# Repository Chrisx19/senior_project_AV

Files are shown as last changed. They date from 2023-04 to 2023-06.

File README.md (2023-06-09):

# CPP Senior Project
Senior project

## December 2022 - May 2023
ROS Noetic control GPS autonomous vehicle using ATMega2560 and Jetson Nano. 

## Video Demo
**Autonomous Mode:**        https://youtu.be/Os8QsEWLSAU

**Controller Mode:**        https://youtu.be/IqCc2zWrYO0

**Test Controller Mode:**   https://youtu.be/60IaMCZQ1AA

### Mechanical 


### Electrical

**PCB Design**
  Reason initial design is included because of the mistakes my team learned while testing. Due to small traces with about 3 Amps going inside of our traces, it blew up and it came out of the PCB. Therefore, we learned from mistakes and calculated how much mil we need for our traces that can withstand about 4 Amps.
  
* **Initial Design: 30 mil traces**



* **Final Design: 150 mil traces**

schematic

Traces

### Software 
* **Communication:** 
  In order to have Jetson Nano and ATMega2560 talk to each other bi directionally, we used a customed UART protocol from ROS package called 'Rosserial.' Rosserial protocol was able to give us the ncecesity we need to transfer data from each other while autonomy. With rosserial, ATMega2560 became its own node and Jetson Nano has its main node and sub node. Nodes are basically scripts, which transfer myriad of data types from node to node.

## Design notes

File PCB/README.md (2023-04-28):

# PCB Design Final


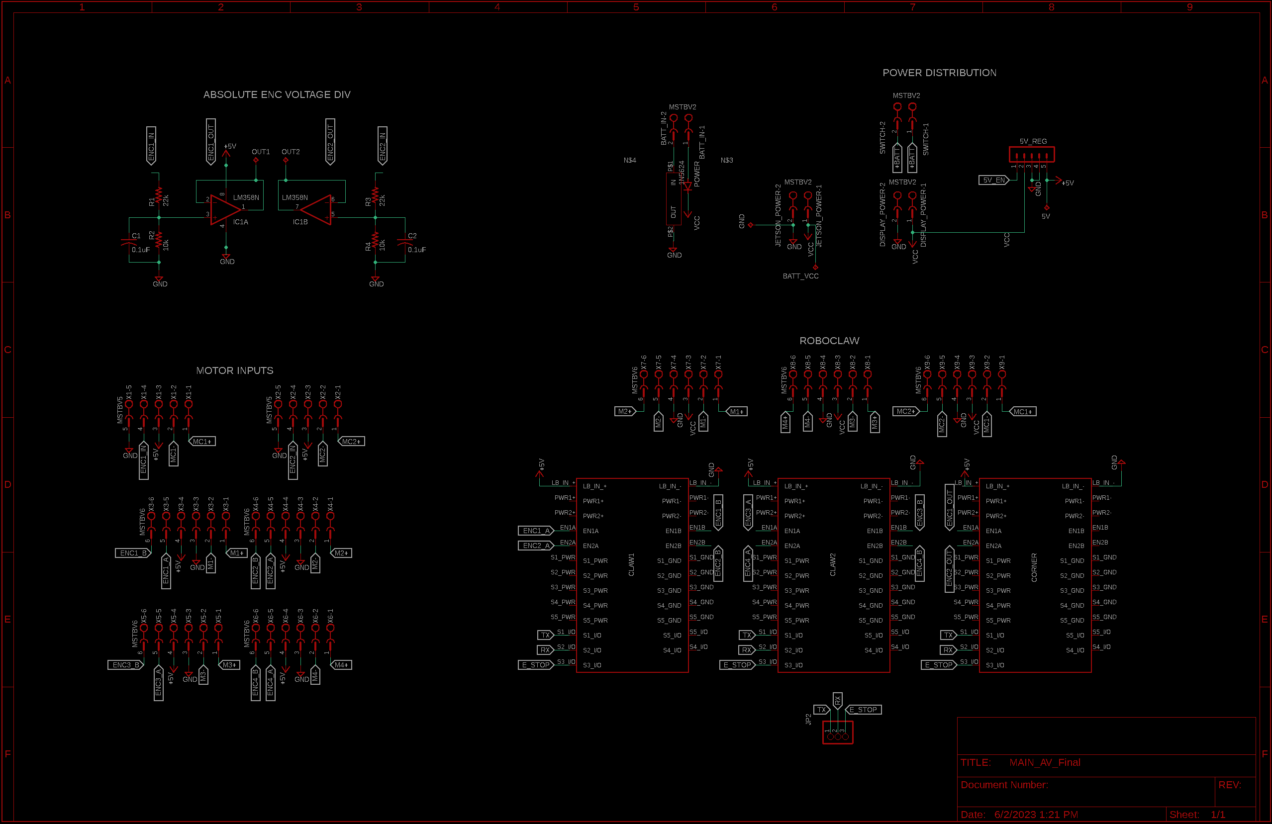
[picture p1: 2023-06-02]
Pictures/schematic.png

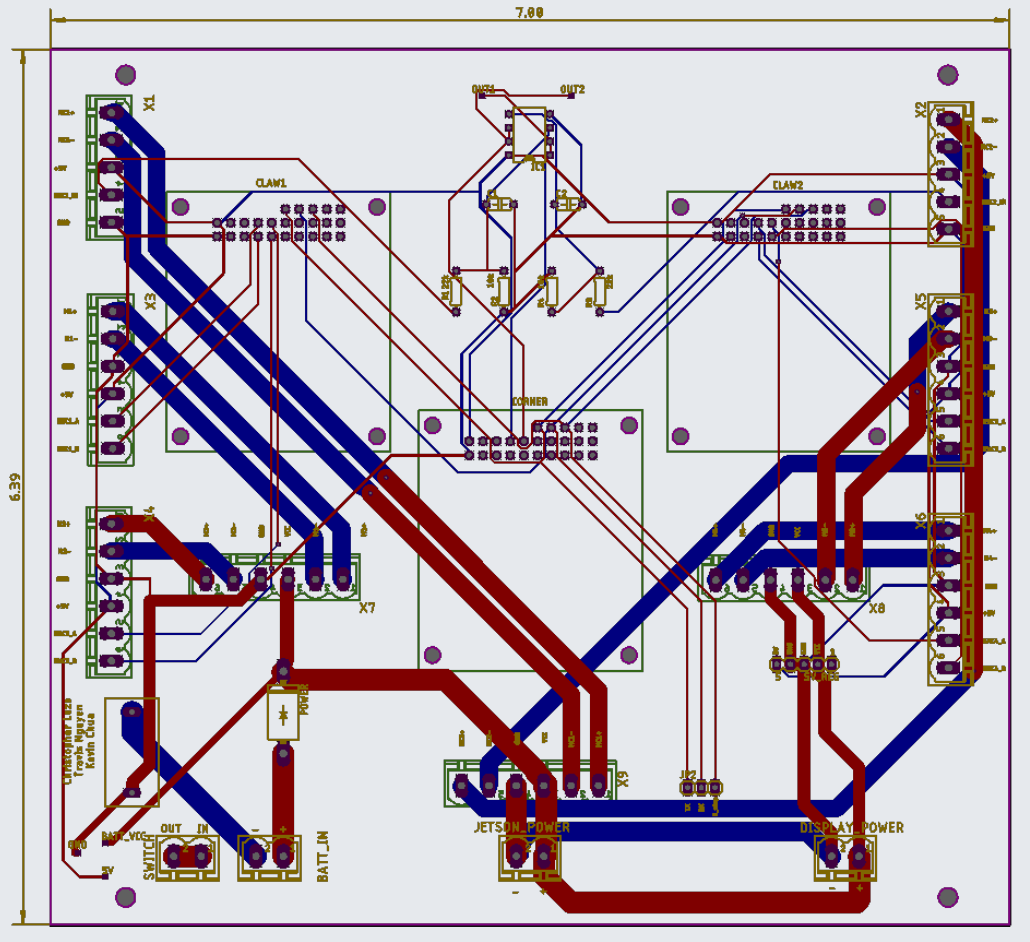
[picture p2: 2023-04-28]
Pictures/Traces.PNG

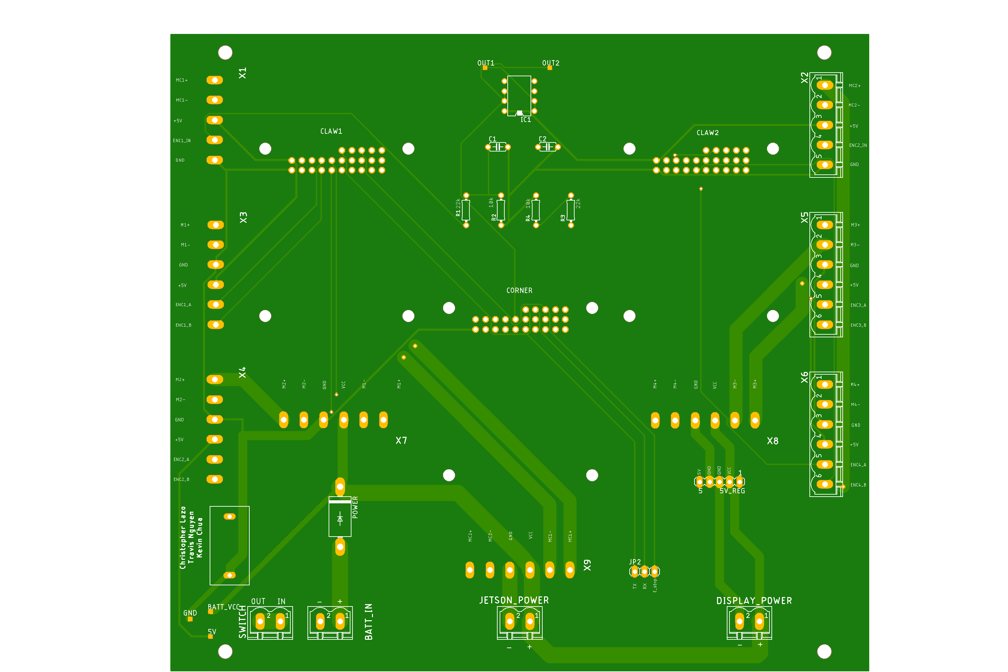
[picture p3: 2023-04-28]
Pictures/Final_Board.png

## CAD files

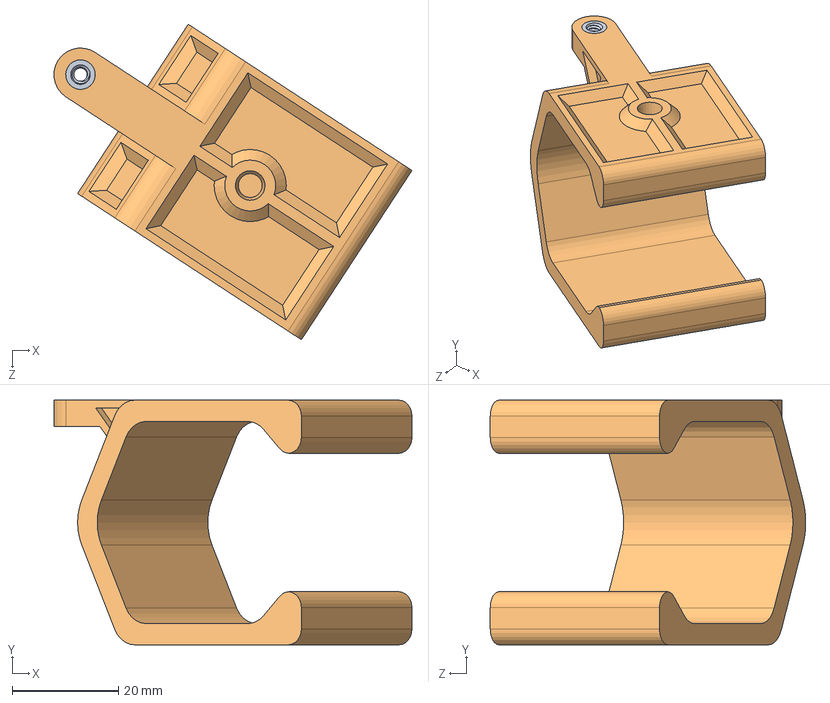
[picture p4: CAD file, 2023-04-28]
Mechanical/Body_senior/3d_printed/Battery holder_5_2mAH.SLDASM
67.3 x 46.0 x 59.3 mm
93365A130_HEAT-SET INSERTS FOR PLASTICS
battery holder_5_2maH

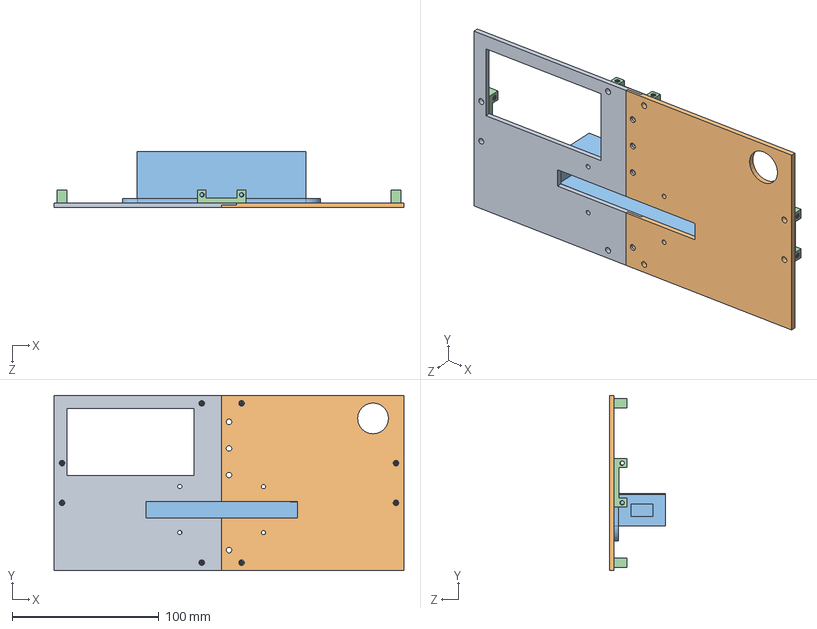
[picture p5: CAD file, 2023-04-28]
Mechanical/Full_Car.SLDASM
238.3 x 119.4 x 38.2 mm
Half_Left_Back
Half_Right_Back
USB_hub_mount
Dual Side Mount_Plate.step x 4

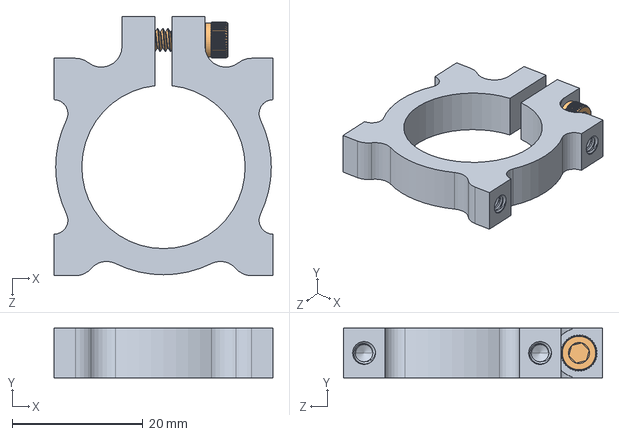
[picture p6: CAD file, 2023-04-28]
Mechanical/wheel_senior/25m Bore Side Tapped Clamping Mount.SLDASM
33.5 x 7.62 x 39.7 mm
25m Bore Side Tapped Clamping Mount
#6-32 0_5 Bolt

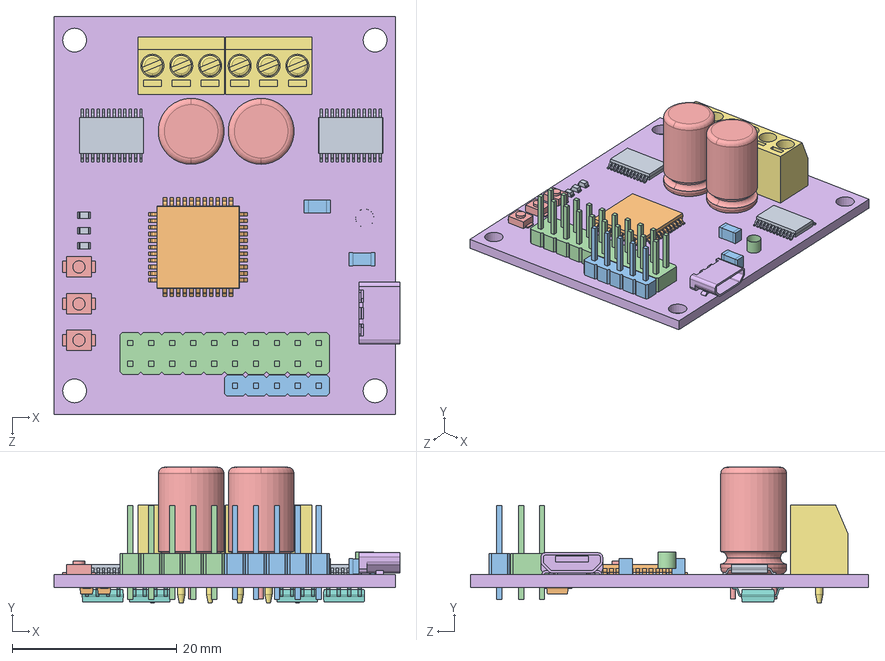
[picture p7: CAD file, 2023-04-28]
Mechanical/Body_senior/electronics/Roboclaw.SLDASM
42.0 x 16.5 x 48.3 mm
404-1004-1-ND x 3
DB2W40200LCT-ND x 2
587-3248-1-ND x 2
SRN5040-220MCT-ND
P15369TB-ND x 2
609-4618-1-ND
ED2636-ND x 2
IRF7351TRPBFCT-ND x 4
620-1319-1-ND x 2
ATXMEGA32A4U-AU-ND
PBC05SAAN
PBC10DAAN
SW1020CT-ND x 3
MC5A-PCB

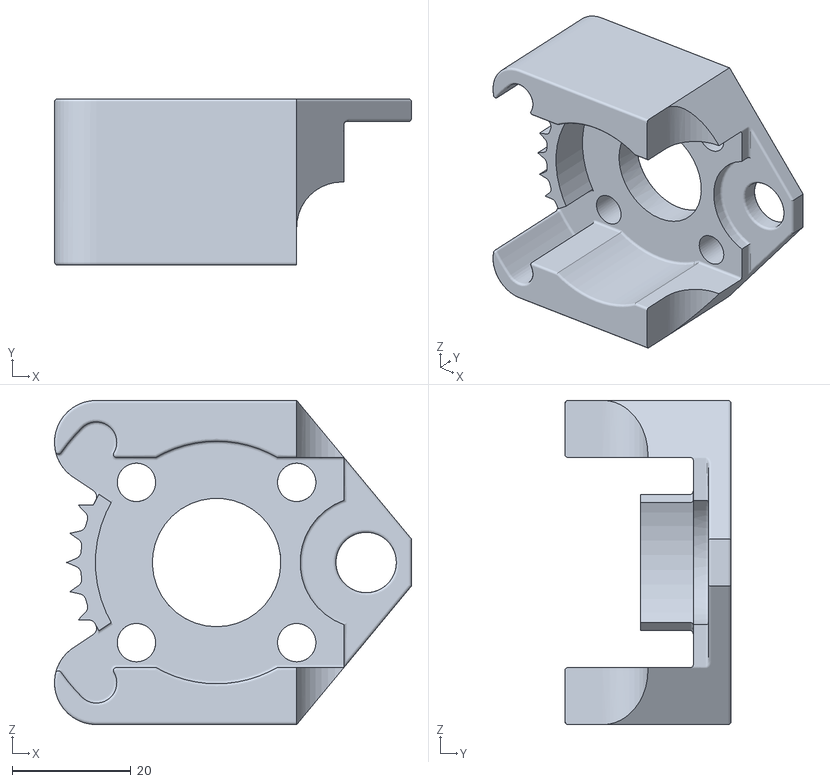
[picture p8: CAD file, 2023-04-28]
3D Parts/Encoder mount.STL
60.0 x 27.9 x 54.5

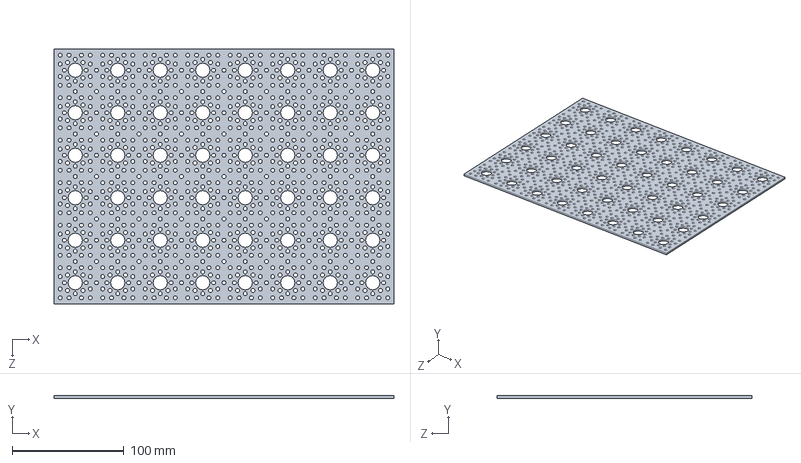
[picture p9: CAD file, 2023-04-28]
Mechanical/Body/9 x 12 Aluminum Pattern Plate.SLDPRT
304.8 x 2.29 x 228.6 mm

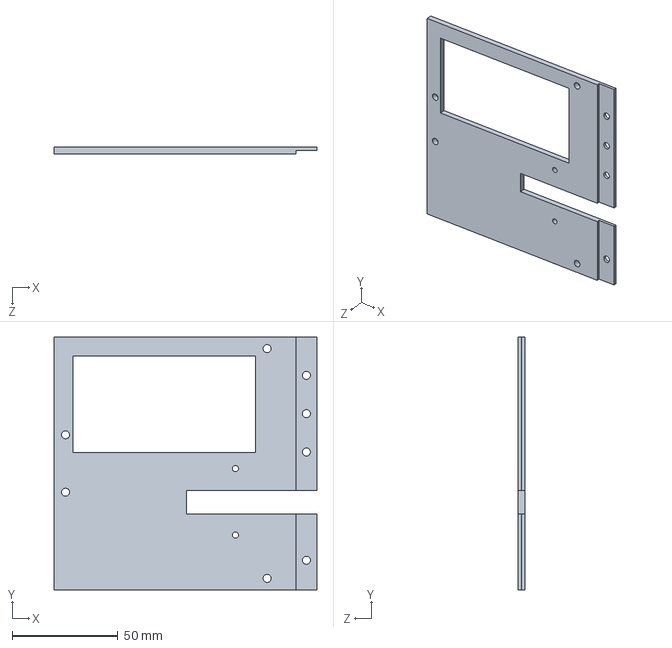
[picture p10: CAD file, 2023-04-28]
Mechanical/Body/Half_Left_Back.SLDPRT
124.2 x 119.4 x 3.17 mm

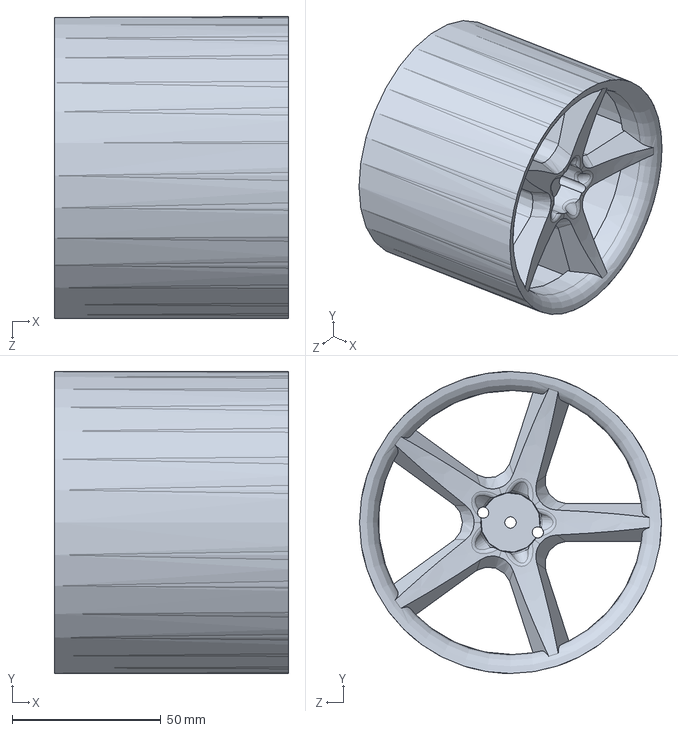
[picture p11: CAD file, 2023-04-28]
Mechanical/wheel_senior/Wheel Rim.sldprt
78.7 x 101.6 x 101.6 mm

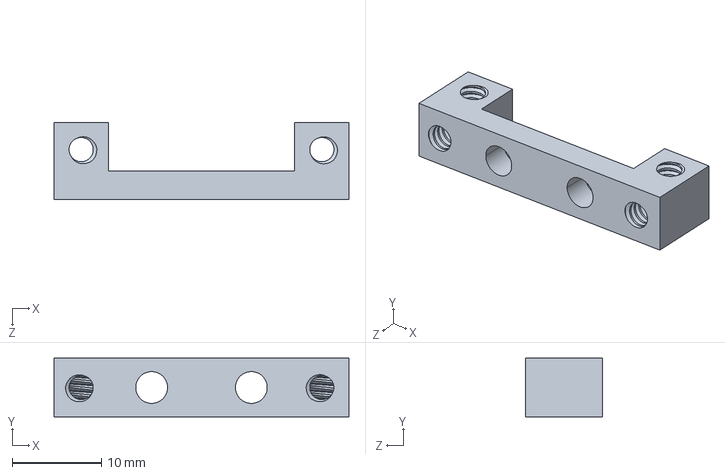
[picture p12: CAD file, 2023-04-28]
Mechanical/Body/Dual Side Mount_Plate.STEP
33.0 x 6.58 x 8.63 mm

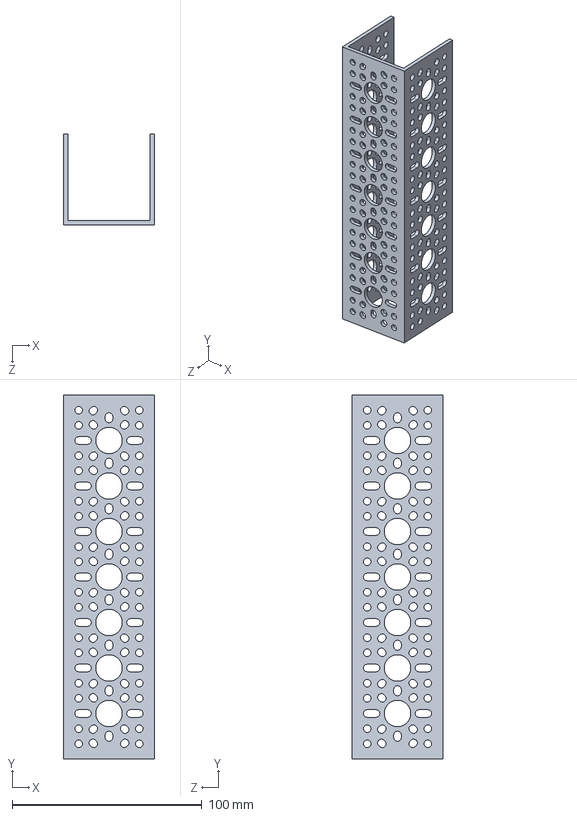
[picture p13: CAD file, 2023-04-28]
Mechanical/wheel_senior/gobilda-7hole-1120series-channel.SLDPRT
48.0 x 192.0 x 48.0 mm

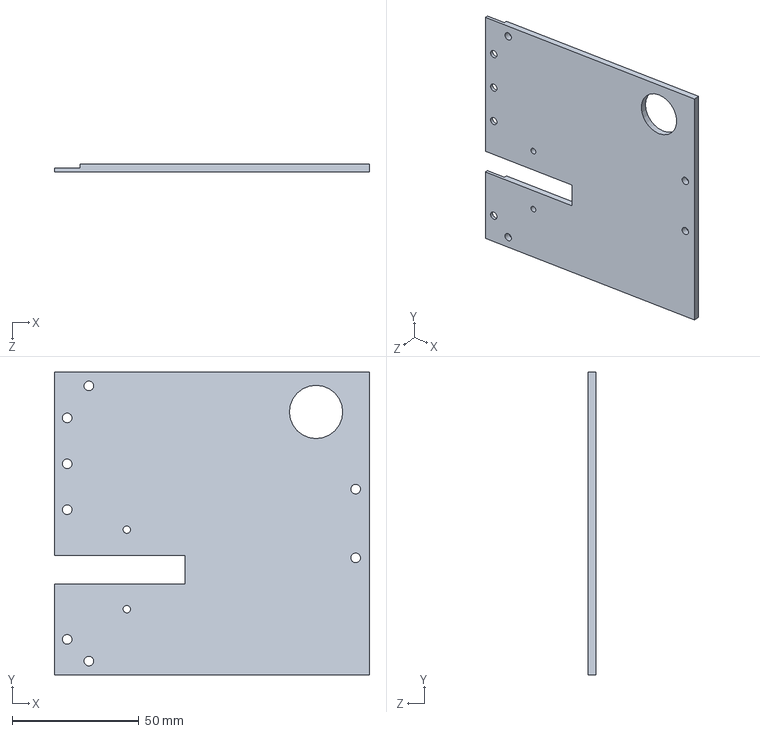
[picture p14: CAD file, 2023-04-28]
Mechanical/Body/Half_Right_Back.SLDPRT
124.2 x 119.4 x 3.18 mm

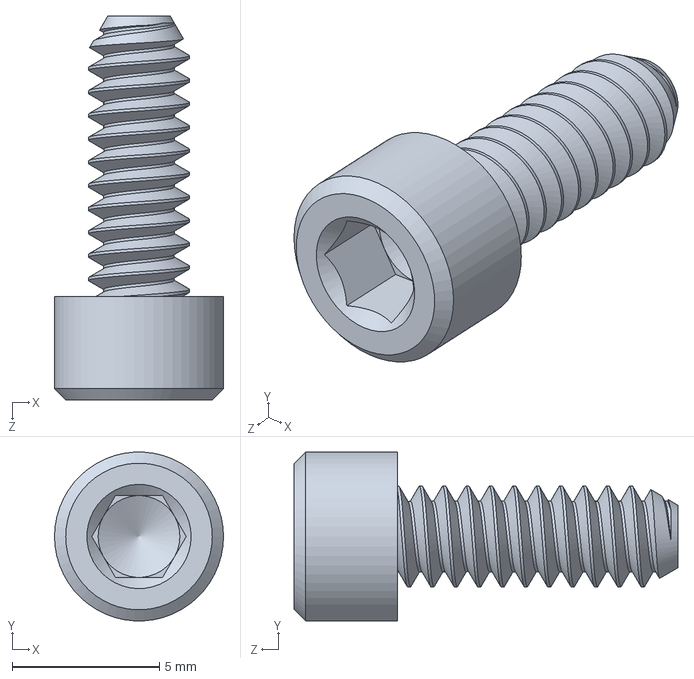
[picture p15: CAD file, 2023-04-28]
Mechanical/wheel_senior/6-32_SHCS.SLDPRT
5.74 x 5.73 x 13.0 mm

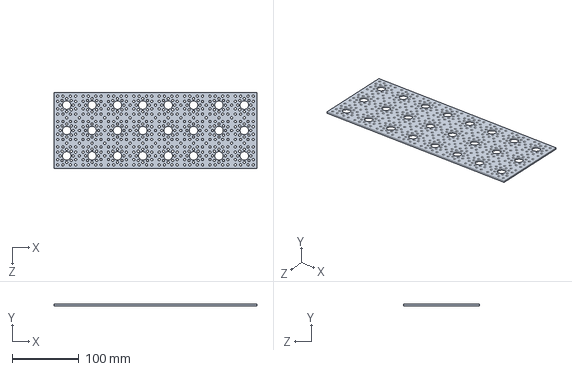
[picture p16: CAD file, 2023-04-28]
Mechanical/Body/4.5 x 12 Aluminum Pattern Plate.SLDPRT
304.8 x 2.29 x 114.3 mm

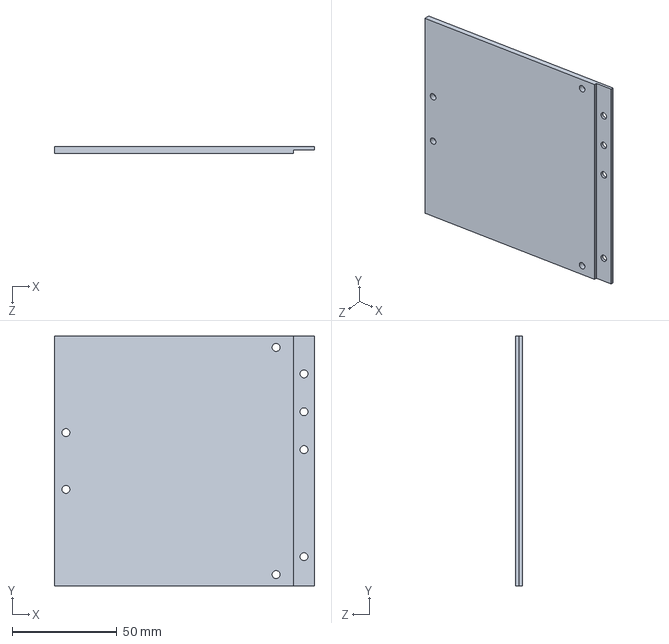
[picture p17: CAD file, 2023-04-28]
Mechanical/Body/Front_Panel_Right.SLDPRT
124.2 x 119.4 x 3.17 mm

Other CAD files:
Mechanical/Body_senior/electronics/SRN5040-220MCT-ND.sldprt
Mechanical/Body_senior/electronics/587-3248-1-ND.sldprt
Mechanical/Body_senior/electronics/DB2W40200LCT-ND.sldprt
Mechanical/Body_senior/electronics/609-4618-1-ND.sldprt
Mechanical/Body/Front_Panel_Left.SLDPRT
Mechanical/Body/Front_Panel_Left.STL
Mechanical/Body/Front_Panel_Right.STL
Mechanical/Body/Half_Left_Back.STL
Mechanical/Body/Half_Right_Back.STL
Mechanical/Body/USB_hub_mount.SLDPRT
Mechanical/Body/USB_hub_mount.STEP
Mechanical/Body/USB_hub_mount.STL
Mechanical/Body/back_panel.STEP
Mechanical/Body/back_panel.STL
Mechanical/Body/front_panel.STEP
Mechanical/Body/front_panel.STL
Mechanical/Body_senior/3d_printed/battery holder_5_2maH.SLDPRT
Mechanical/Body_senior/3d_printed/battery holder_5_2maH.STL
Mechanical/Body_senior/control_board/91255A077_ALLOY STEEL BUTTON-HEAD SOCKET CAP SCREW.SLDPRT
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

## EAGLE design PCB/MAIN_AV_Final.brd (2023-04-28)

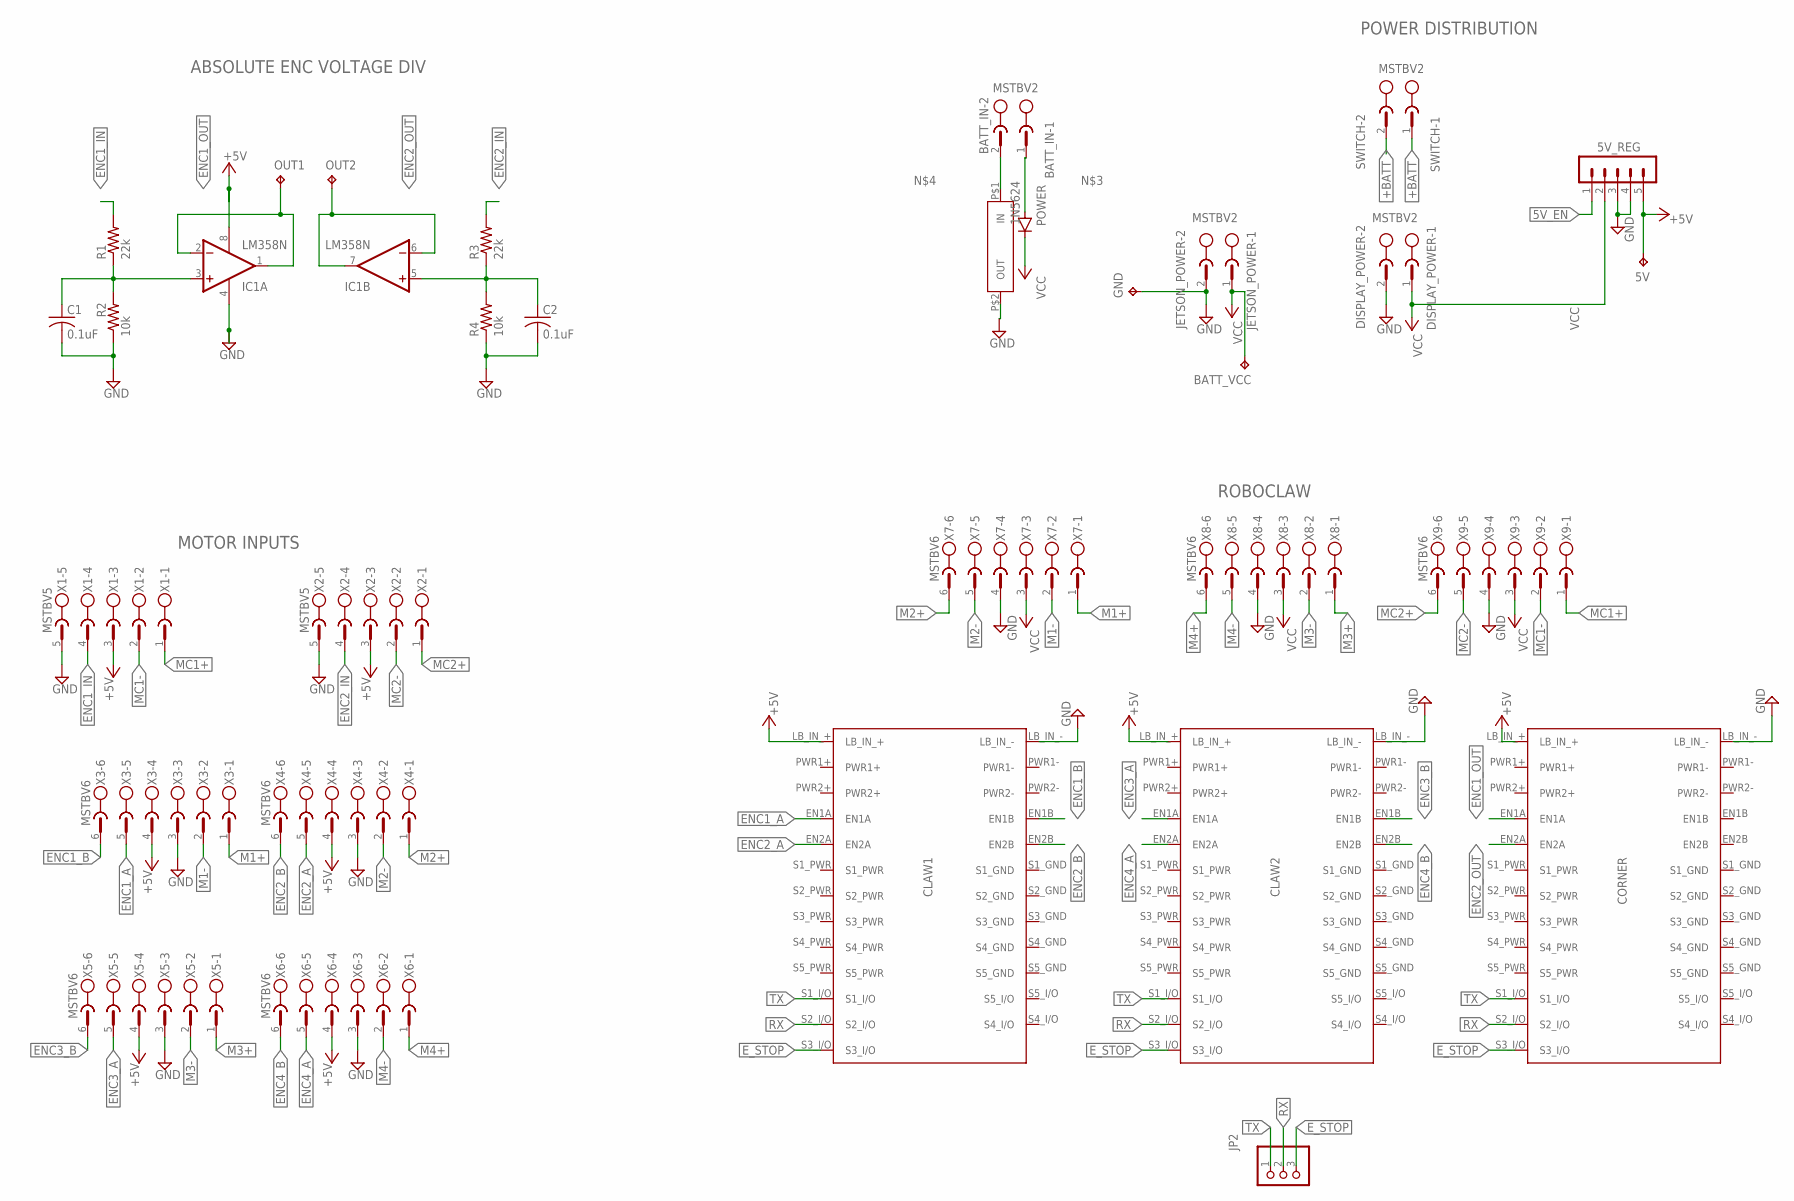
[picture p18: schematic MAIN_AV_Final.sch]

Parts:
5V: TPTP10SQ; TP10SQ
5V_REG: MA05-1
BATT_IN: MSTBV2
BATT_VCC: TPTP10SQ; TP10SQ
C1, C2: 0.1uF; C050-024X044
CLAW1, CLAW2: ROBOCLAW2X7A; ROBOCLAW
CORNER: ROBOCLAW2X7A; ROBOCLAW
DISPLAY_POWER: MSTBV2
GND: TPTP10SQ; TP10SQ
IC1: LM358N; DIL08
JETSON_POWER: MSTBV2
JP2: PINHD-1X3; 1X03
OUT1, OUT2: TPTP10SQ; TP10SQ
POWER: 1N5624; DO201-15
R1, R3: 22k; 0204/7
R2, R4: 10k; 0204/7
SWITCH: MSTBV2
U$1: FUSEHOLDER
X1, X2: MSTBV5
X3, X4, X5, X6, X7, X8, X9: MSTBV6

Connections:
5V_EN: 5V_REG.1
+5V: 5V.TP, 5V_REG.5, CLAW1.LB_IN_+, CLAW2.LB_IN_+, CORNER.LB_IN_+, IC1.8 (V+), X1.3, X2.3, X3.4, X4.4, X5.4, X6.4
+BATT: SWITCH.1, SWITCH.2
ENC1_A: CLAW1.EN1A, X3.5
ENC1_B: CLAW1.EN1B, X3.6
ENC1_IN: R1.2, X1.4
ENC1_OUT: CORNER.EN1A, IC1.1 (OUT), IC1.2 (-IN), OUT1.TP
ENC2_A: CLAW1.EN2A, X4.5
ENC2_B: CLAW1.EN2B, X4.6
ENC2_IN: R3.2, X2.4
ENC2_OUT: CORNER.EN2A, IC1.6 (-IN), IC1.7 (OUT), OUT2.TP
ENC3_A: CLAW2.EN1A, X5.5
ENC3_B: CLAW2.EN1B, X5.6
ENC4_A: CLAW2.EN2A, X6.5
ENC4_B: CLAW2.EN2B, X6.6
E_STOP: CLAW1.S3_I/O, CLAW2.S3_I/O, CORNER.S3_I/O, JP2.3
GND: 5V_REG.3, 5V_REG.4, C1.2, C2.2, CLAW1.LB_IN_-, CLAW2.LB_IN_-, CORNER.LB_IN_-, DISPLAY_POWER.2, GND.TP, IC1.4 (V-), JETSON_POWER.2, R2.1, R4.1, U$1.P$2 (OUT), X1.5, X2.5, X3.3, X4.3, X5.3, X6.3, X7.4, X8.4, X9.4
M1+: X3.1, X7.1
M1-: X3.2, X7.2
M2+: X4.1, X7.6
M2-: X4.2, X7.5
M3+: X5.1, X8.1
M3-: X5.2, X8.2
M4+: X6.1, X8.6
M4-: X6.2, X8.5
MC1+: X1.1, X9.1
MC1-: X1.2, X9.2
MC2+: X2.1, X9.6
MC2-: X2.2, X9.5
unnamed: C1.1, IC1.3 (+IN), R1.1, R2.2
unnamed: C2.1, IC1.5 (+IN), R3.1, R4.2
unnamed: BATT_IN.1, POWER.A
unnamed: BATT_IN.2, U$1.P$1 (IN)
RX: CLAW1.S2_I/O, CLAW2.S2_I/O, CORNER.S2_I/O, JP2.2
TX: CLAW1.S1_I/O, CLAW2.S1_I/O, CORNER.S1_I/O, JP2.1
VCC: 5V_REG.2, BATT_VCC.TP, DISPLAY_POWER.1, JETSON_POWER.1, POWER.C, X7.3, X8.3, X9.3

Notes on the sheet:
ABSOLUTE ENC VOLTAGE DIV
POWER DISTRIBUTION
MOTOR INPUTS
ROBOCLAW

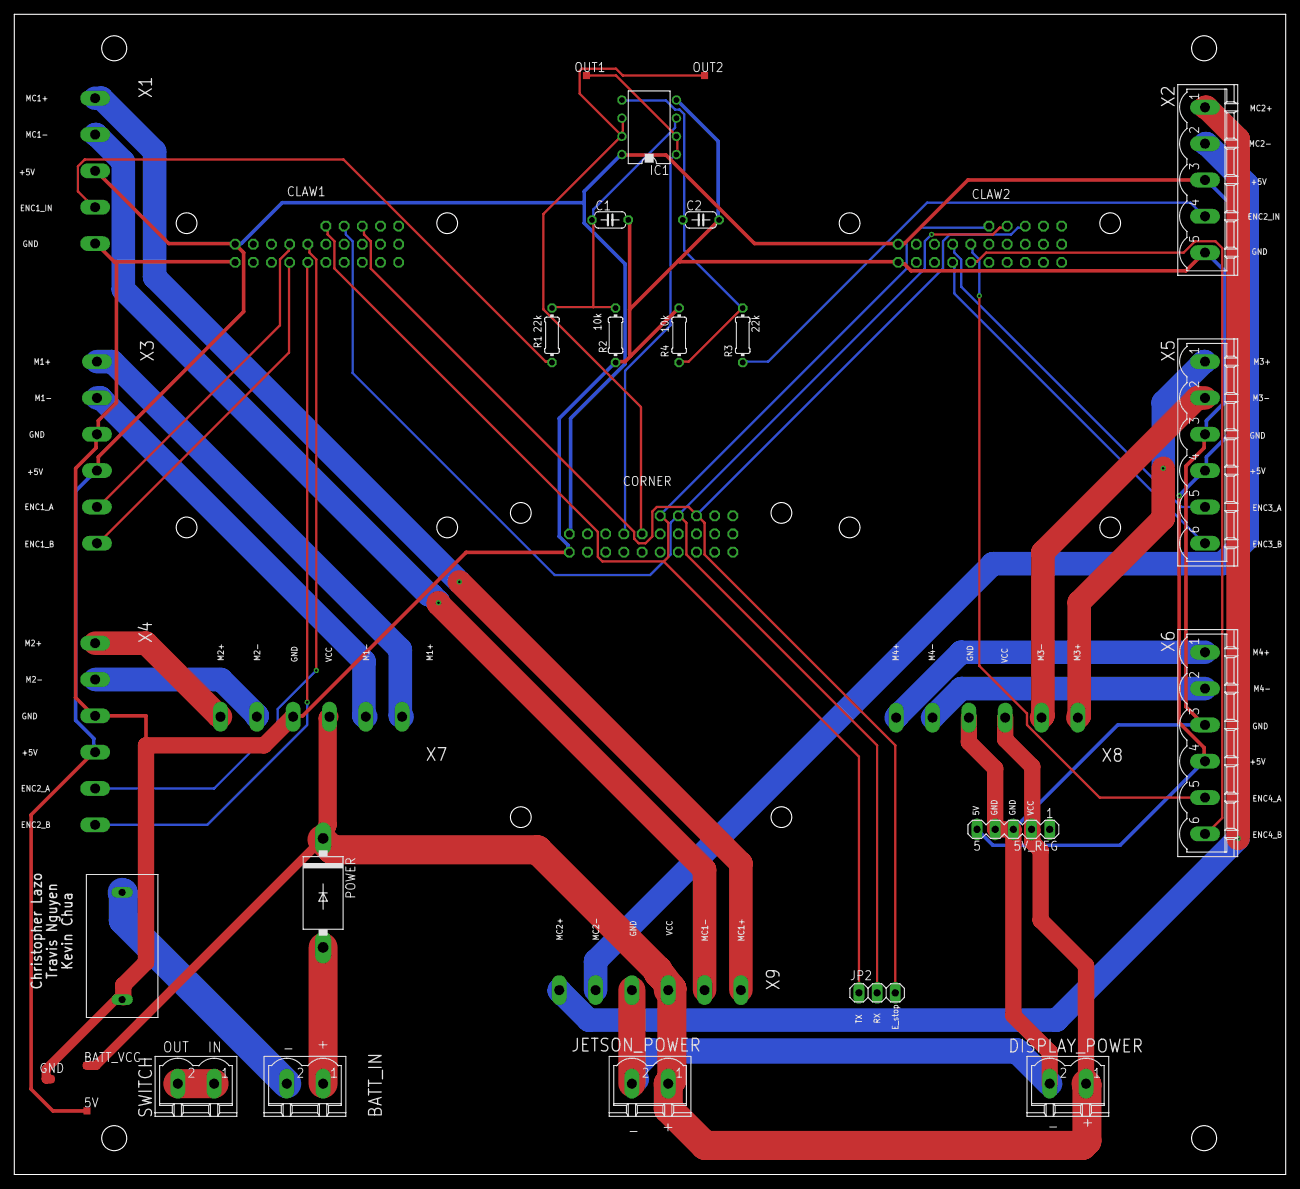
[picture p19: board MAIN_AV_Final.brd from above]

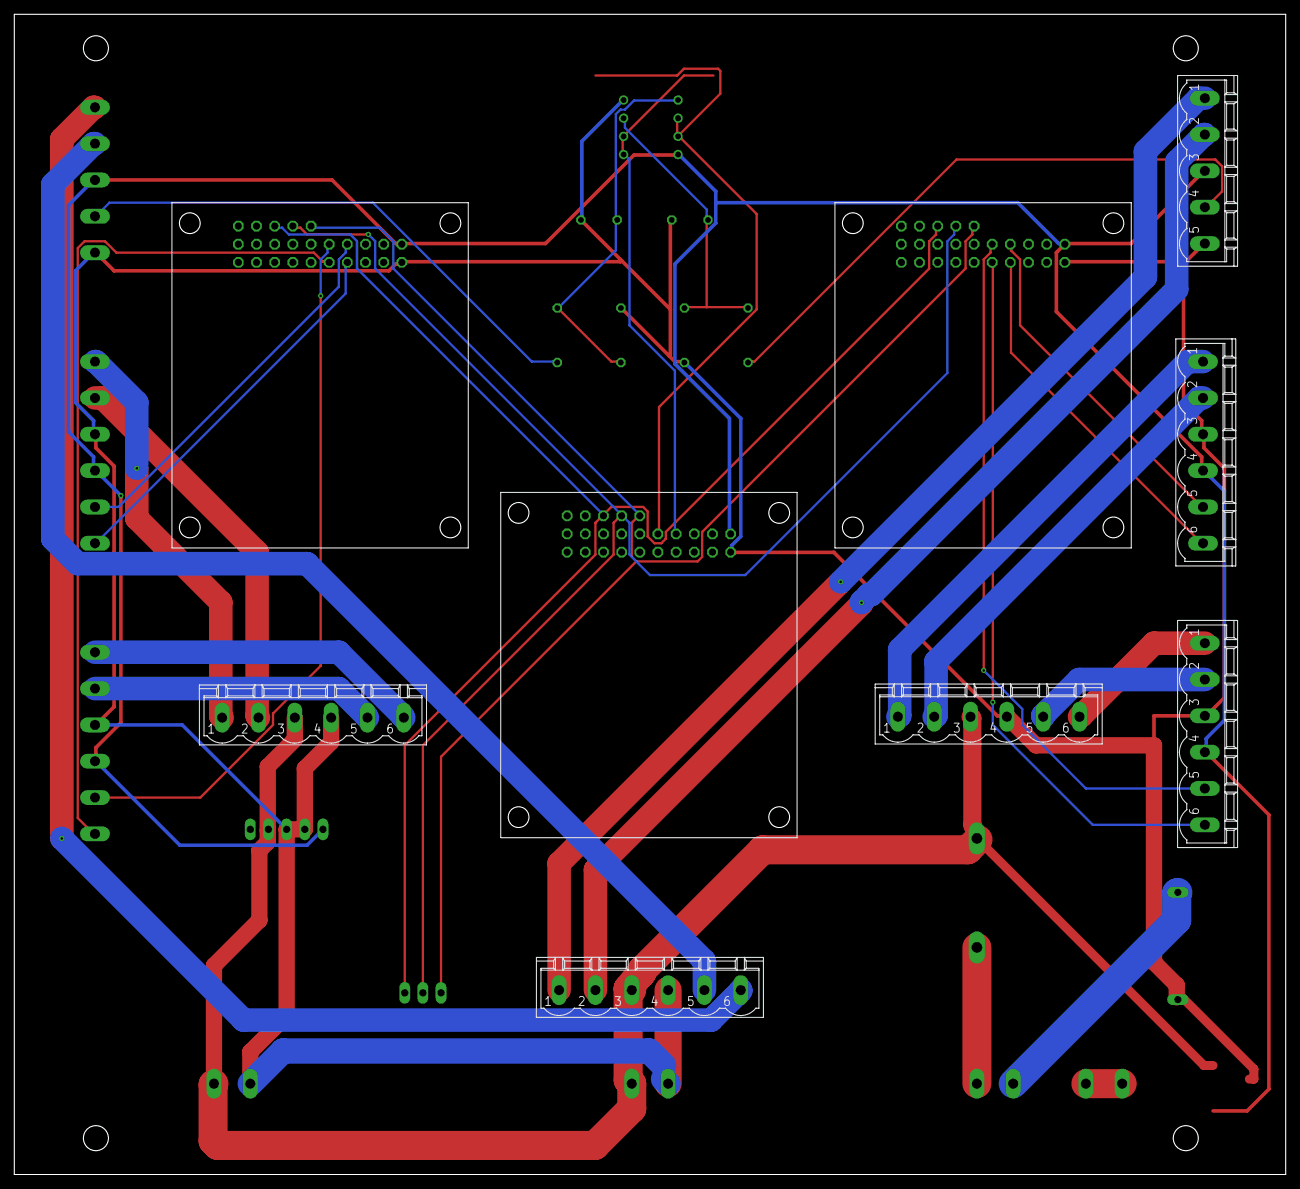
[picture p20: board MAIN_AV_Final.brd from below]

Board: 2 copper layers, 177.8 x 162.2 mm, 32 parts (9 on the bottom side), 35 nets.

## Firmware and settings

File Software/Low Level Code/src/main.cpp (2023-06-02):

#include <ros.h>
#include <geometry_msgs/Twist.h>
#include <std_msgs/Int32.h>
#include <std_msgs/Float32.h>
#include <std_msgs/Bool.h>
#include <av_senior/Arduino_telemetry.h>
#include <SoftwareSerial.h>
#include "RoboClaw.h"
#include <math.h>

#define address1 0x80
#define address2 0x81
#define address3 0x82     //corner_motor

#define accel 1000

const int trig1 = 12;
const int echo1 = 13;

const int analog_in_right = A0;
const int analog_in_left = A1;

int16_t g_drive_duty_cycle = 0;
int16_t g_corner = 0;
int16_t g_turn= 0;

bool manual_controller = true;
bool en = false;

int right_sensor, middle_sensor, left_sensor;


// ros::NodeHandle  nh;
ros::NodeHandle_<ArduinoHardware, 5, 5, 512, 512> nh;

SoftwareSerial serial(10, 11);     //serial (rx, tx) can use pin 6 for tx
RoboClaw roboclaw(&serial, 10000); //10000
//==========================================================================Global================================================================================
void AV_vel_cb(const geometry_msgs::Twist& AV_vel_msg);
void AV_manual_en_cb(const std_msgs::Bool& AV_vel_manual_msg);
void corner_drive(int turn, int drive);
void motor_stop(void);
int sensor1(int delay_sonar);
void publishSpeed(int time);

ros::Subscriber<geometry_msgs::Twist> AV_vel_sub("cmd_vel_AV", &AV_vel_cb);
ros::Subscriber<std_msgs::Bool> AV_manual_EN_sub("manual_en", &AV_manual_en_cb);

av_senior::Arduino_telemetry distance_data;
ros::Publisher distance_pub("distance_ll", &distance_data);
//==========================================================================Setup and Loop================================================================================
void setup()
{
  roboclaw.begin(115200);
  // nh.getHardware()->setBaud(38400);
  motor_stop();
  pinMode(trig1, OUTPUT);
  pinMode(echo1, INPUT);

  nh.initNode();
  // nh.advertise(distance_pub);
  nh.subscribe(AV_vel_sub);
  nh.subscribe(AV_manual_EN_sub);
}

void loop()
{
  right_sensor = analogRead(analog_in_right);
  middle_sensor = sensor1(500);
  left_sensor = analogRead(analog_in_left);
 
  if (manual_controller == false)
  {
    g_drive_duty_cycle = 550;

    if (middle_sensor < 40)
    {
      g_turn = 500;
      // Object in front and to the right => g_turnLeft
      if(right_sensor > 150 && middle_sensor < 30)
      {
        g_turn = -250; // Turn half left
      }
      // Object in front and to the left => Turn Right
      else if(middle_sensor < 30 && left_sensor > 150)
      {
        g_turn = 250; // Turn half right
      }
      // Object is close to all sensors => Reverse or go backwards
      else if(right_sensor > 150 && middle_sensor < 20 && left_sensor > 150)
      {
        g_turn = 0; // Set Turn angle to 0 or face straight
        g_drive_duty_cycle = -300; // Set reverse speed to 1/4 of max speed
      }
      // Object very close to right side => Turn Hard Left 
    }
    else if (right_sensor > 100)
    {
      g_turn = -250;
    }
    else if (left_sensor > 100)
    {
      g_turn = 250;
    }
    g_corner = turn + 780;
    corner_drive(g_corner, g_drive_duty_cycle);
  }

  // publishSpeed(10);

  nh.spinOnce();
  // delay(1);
}

//==========================================================================Functions================================================================================

void publishSpeed(int time)
{
  distance_data.Right_Distance = right_sensor;
  distance_data.Mid_Distance   = middle_sensor;
  distance_data.Left_Distance  = left_sensor;
  delay(time);
  distance_pub.publish( &distance_data);
}

int sensor1(int delay_sonar)
{
  digitalWrite(trig1, LOW);
  delayMicroseconds(delay_sonar);
  digitalWrite(trig1, HIGH);
  delayMicroseconds(delay_sonar);
  digitalWrite(trig1, LOW);

  long time = pulseIn (echo1, HIGH);
  int cm_distance = (time / 29.1 / 2);
  return cm_distance;
}

void AV_manual_en_cb(const std_msgs::Bool& AV_vel_manual_msg)
{
  manual_controller = AV_vel_manual_msg.data;
}

void AV_vel_cb(const geometry_msgs::Twist& AV_vel_msg)  //callback function from subscribe
{
  g_drive_duty_cycle = AV_vel_msg.linear.x;           //val: -2800 <-> 2800
  g_turn = AV_vel_msg.angular.z;
  g_corner = turn + 780;          //middle: 780

    if (manual_controller)
    {
      corner_drive(corner, g_drive_duty_cycle);
    }

}//end fo AV_vel_cb

void corner_drive(int turn, int drive)
{
  float accel_rate = 1.5;
  float accel_max = pow(2,15)-1;
  int corner_accel = accel_max * accel_rate;

  if (turn < 780)
  {
    roboclaw.SpeedAccelDeccelPositionM1(address3, corner_accel, 1000, corner_accel, turn, 1);    //Right_Corner    //  roboclaw.SpeedAccelDeccelPositionM1(address3,26213,1000,26213,6,1);    //Right_Turn
    roboclaw.SpeedAccelDeccelPositionM2(address3, corner_accel, 1000, corner_accel, turn, 1);                      //  roboclaw.SpeedAccelDeccelPositionM2(address3,26213,1000,26213,7,1);
    
    roboclaw.SpeedAccelM1M2(address1, accel, drive * 1/2, drive * 1/2);
    roboclaw.SpeedAccelM1M2(address2, accel, drive, drive);
  
  }
  else if (turn > 780)
  {
    roboclaw.SpeedAccelDeccelPositionM1(address3, corner_accel, 1000, corner_accel, turn, 1);   //Left_Corner       //  roboclaw.SpeedAccelDeccelPositionM1(address3,26213,1000,26213,1559,1);    //Left_Turn 
    roboclaw.SpeedAccelDeccelPositionM2(address3, corner_accel, 1000, corner_accel, turn, 1);                       //  roboclaw.SpeedAccelDeccelPositionM2(address3,26213,1000,26213,1564,1);
  
    roboclaw.SpeedAccelM1M2(address1, accel, drive, drive);
    roboclaw.SpeedAccelM1M2(address2, accel, drive * 1/2, drive * 1/2);
  }
  else
  {
    roboclaw.SpeedAccelDeccelPositionM1(address3, corner_accel, 1000, corner_accel, 777, 1);  //Middle_Corner
    roboclaw.SpeedAccelDeccelPositionM2(address3, corner_accel, 1000, corner_accel, 750, 1);
    roboclaw.SpeedAccelM1M2(address1, accel, drive, drive);
    roboclaw.SpeedAccelM1M2(address2, accel, drive, drive);
  }
}//end of corner_drive

void motor_stop(void)
{
  uint8_t rc[3] = {address1, address2, address3};
  for(int i = 0; i < 3; i++)
  {
    roboclaw.SpeedAccelM1M2(rc[i], 2800, 0, 0);
  }
}//end of motor_stop
